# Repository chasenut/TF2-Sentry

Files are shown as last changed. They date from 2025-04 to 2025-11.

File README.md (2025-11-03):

<div align="center">

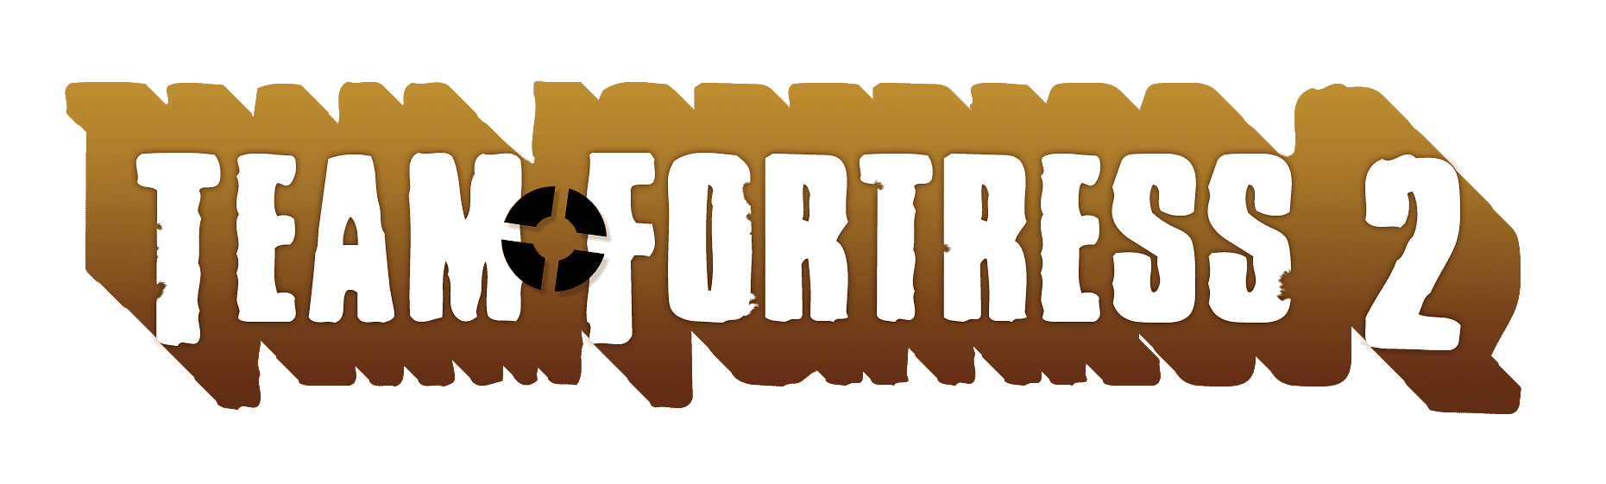
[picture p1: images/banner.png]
banner


<br>

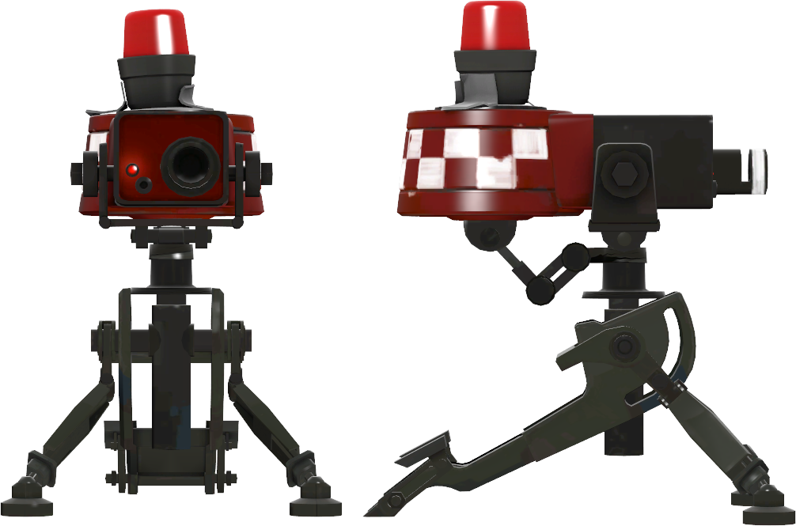
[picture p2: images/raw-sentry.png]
sentry


<br>
<br>

Team Fortress 2 Sentry (Level 1).<br>
3D print your own and upgrade it!

</div>

<br>

<div align="center">
    
# About

<br>

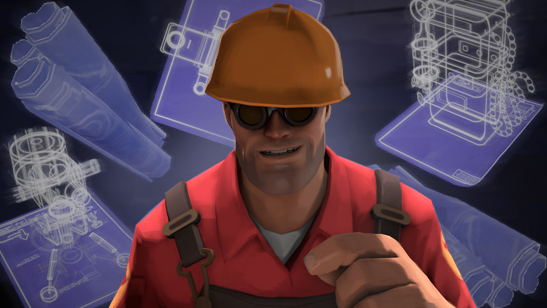
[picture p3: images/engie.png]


</div>

<br>
<br>

I started this project in February, 2025, after Valve announced open-sourcing Team Fortress 2.<br>
This is the piece of software I grew up with, so to commit something to the community, 
I made this project which includes self-made 3D CADs and some electronics. <br>
This took hundreds of hours to make, and spanned over several months to design and make.

<br>

**Feel free to do whatever you want with it!**

## Parts

Microcontroller: `esp32doit-devkit-v1`<br>
I'm using some standard servos and motors, as well as LEDs etc. <br>
All (electronic) parts can be purchased at [botland.com.pl](https://www.botland.com/pl).<br>
Everything (that could be) is 3D-printed. I made all models myself.<br>
This version of the turret 
**doesn't require any custom metal parts, everything is 3D-printable** 
and screw together using only M3 and M4 machine screws.<br>
All (printable) models should be in `parts/` directory.<br>
You can also preview the 3D model [here](https://a360.co/44RaSrK).<br>
<br>

### Needed (store bought) parts

You may need these parts:
- (3) Metal bearings `6004/2RS` (or any other model, only important thing are dimensions)
- (2) Standard servos `MG995` or `MG996R` or any standard servo that fit. **Note here**, I found these
to be a little to weak (and they don't really handle the weight of everything). I recommend finding
a stronger ones with the same dimensions
- (2) Servo horns (metal is recommended), must work with your servo, something like [these](https://www.amazon.com/Honbay-Aluminum-Standard-Airplane-Hop-up/dp/B09CT7QK6C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)
- (A lot of) `M3` and `M4` machine screws of different lengths, preferebly `10, 15, 20, 30 [mm]`
- (2) Red 8mm LED diodes
- (1) Red 6mm Laser diode (like [this](https://www.amazon.com/HiLetgo-10pcs-650nm-Diode-Laser/dp/B071FT9HSV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))
- (1) Red Siren (**to steal 2 parts nice parts from, **red transparent head** and **reflective dish**), [this one](https://www.amazon.com/Car-Siren-Strobe-Light-Rotation/dp/B0DL5T3F2J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)
- (1) Mini Motor, I used `N20-BT39 micro 1000:1 32RPM - 9V` ([mine here](https://botland.com.pl/silniki-micro-n20-seria-mp-medium-power/12601-silnik-n20-bt39-micro-10001-32rpm-9v-5904422377151.html)) 
but you may use any other of your choice (similar specs, same size), it is for siren to spin.

<br>
Of course you may also need some batteries, wires and other circuit-stuff. Not gonna lie, I didn't do the circuit stuff the best way, 
so you can definetly do better than me.

### Printing & Filaments

I used `Polymaker Polyterra` filament (1.75):
- [Matte Lava Red](https://www.amazon.com/Polymaker-PolyTerra-Bioplastic-Printing-Filament/dp/B08QMDD6NP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)
- [Matte Charcoal Black](https://www.amazon.com/Polymaker-PolyTerra-Bioplastic-Printing-Filament/dp/B08QMBPZBF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)

One spool of `red` filament is enough (1kg), but you may need a few of the `black`s, 
I used about 3-4 (kg) of those.

For **printing** I used `Bambu Lab P1S`, **no need for AMS** module. <br>
Everything is printed on `0.08 mm` layer height, I used default `Bambu Studio` presets.<br>

### Contact

For any additional info and contribution, please contanct me:

***Email***
- `switalamaciej5[at]gmail.com`

***Discord***
- `cashtan`

***Github***
- `chasenut`

## Some fun specs

This Sentry:
- Has a maximum height of about `55cm` or `21.6"`
- Is heavy (weighs a couple of solid pounds)
- Took a few (whole) days just to print the parts
- Uses many many screws
- Takes about 30-60 minutes just to dis/assemble
- Has a spinning sirent with LED
- Has a front LED and LED Laser
- Is capable of rotation:
    - vertical elevation/depression
    - horizontal traverse
- Has several moving parts

<div align="center">

# Gallery

<br>

_The white stand is not needed, it is just for display_

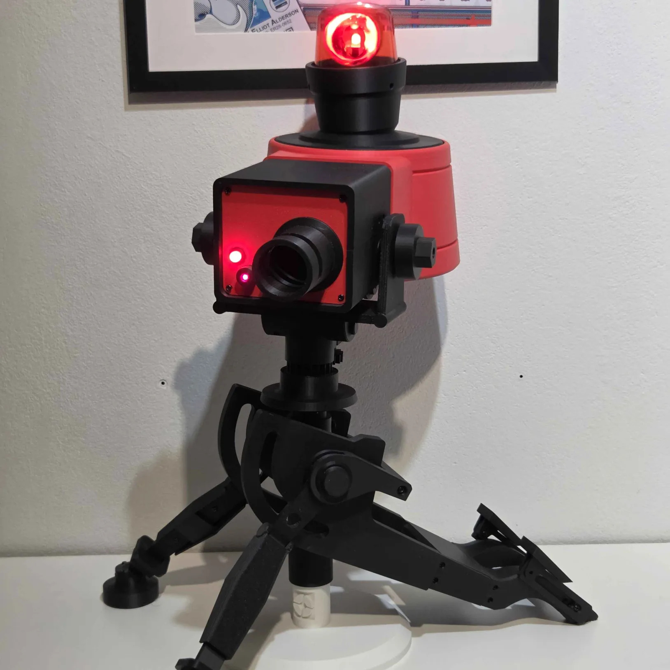
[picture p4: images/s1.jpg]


<br>

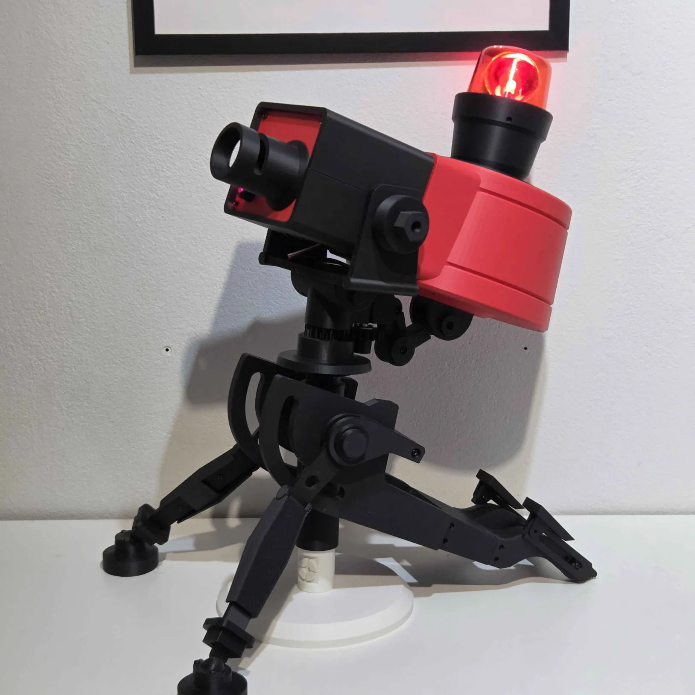
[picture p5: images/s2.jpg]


<br>

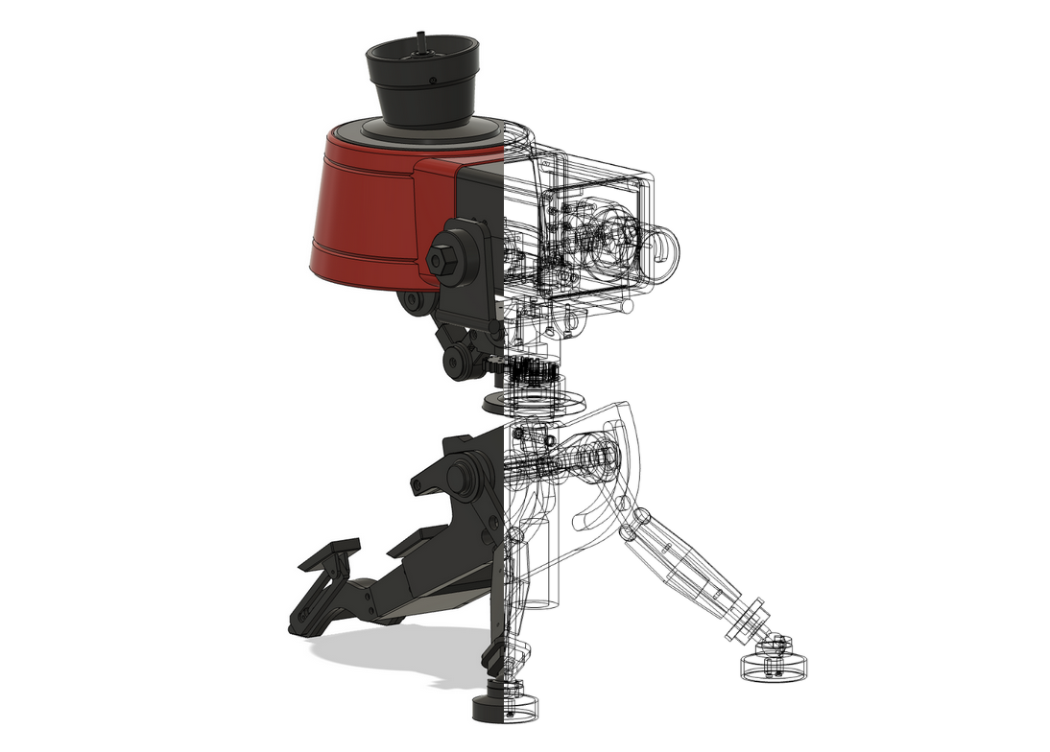
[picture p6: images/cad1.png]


</div>

<br>

# Functionality & code

This project's goal was to create a **3D replica** of Sentry from our beloved game Team Fortress 2.
Code for this Sentry _(and wireless module (Wrangler), which is not yet finished)_ isn't complete, full or outstanding, 
I would say it was just a placeholder and was assembled in a short period of time just to test the turret. **Feel free** to make/submit
your own code for this project, you can use current one as reference. 

# Code build

For building and deploying I use(d) VSC's [Platformio](https://platformio.org/).

---

<div align="center">
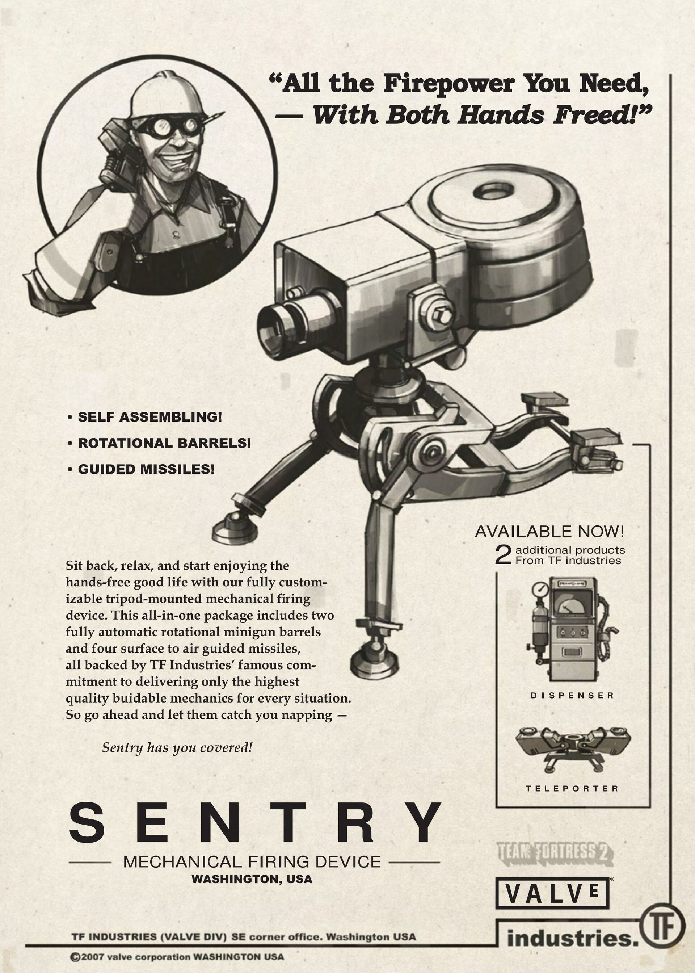
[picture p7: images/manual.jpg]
manual
    
</div>

---

## Notice

Every single parts is self-designed, none content were copied.
Inspired by [Mr. Volt](https://www.youtube.com/@MrVolt).

This project is not affiliated with Valve Corporation.
Image sources:
- [teamfortress.com](https://www.teamfortress.com)
- [mundymundy.tumblr.com](https://mundymundy.tumblr.com/post/672858009940213760/hello-can-you-do-general-relationship-headcanons)

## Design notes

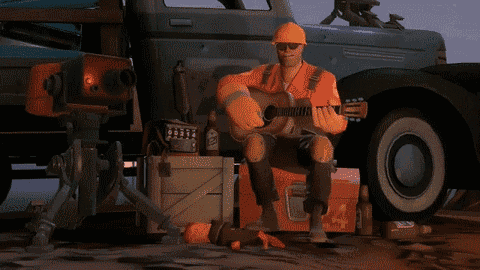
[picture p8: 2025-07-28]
images/guitar.gif

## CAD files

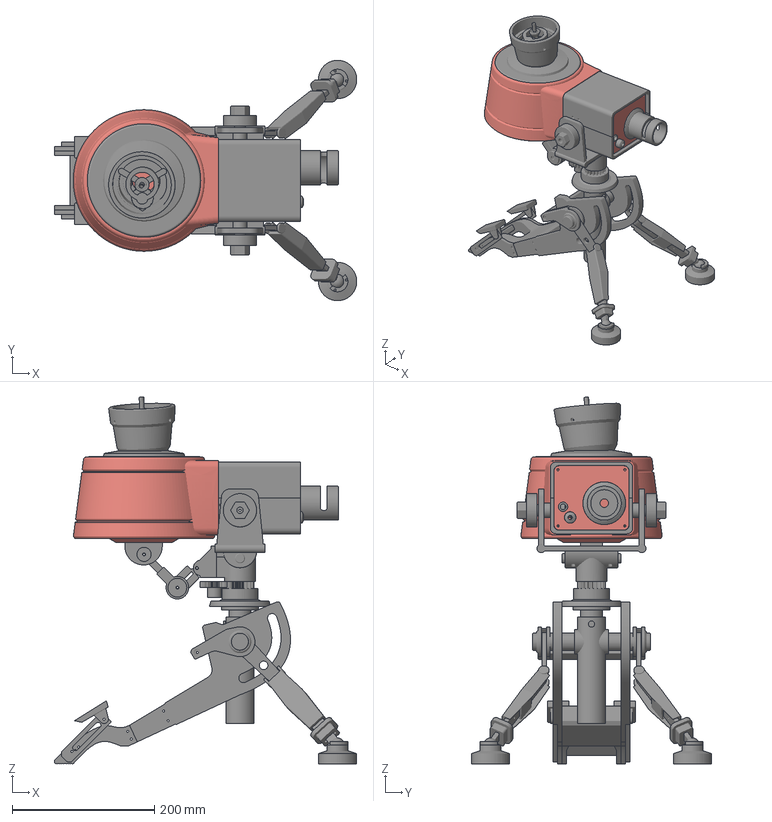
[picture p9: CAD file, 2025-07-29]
parts/TF2-Sentry-chasenut-v1-129.3mf
425.7 x 338.3 x 516.5 mm
backleg_bridge
backleg_mp_1
backleg_mp_2
backleg_smaller_bridge
backleg_sp_1
backleg_sp_2
bearing_chamber_1
bearing_chamber_2
bottom_shaft
cyl_shaft
frontleg_ball1
frontleg_ball2
frontleg_ballfence1
frontleg_ballfence2
frontleg_big_collar1
frontleg_big_collar2
frontleg_bottom1_1
frontleg_bottom1_2
frontleg_bottom2_1
frontleg_bottom2_2
frontleg_leg1
frontleg_leg2
frontleg_lower_collar1
frontleg_lower_collar2
hex_shaft
servo1_mount
servo_horn_visual
spine
thing1_1
thing1_2
thing2_1
thing2_2
up_collar1_1
up_collar1_2
up_collar2_1
up_collar2_2
up_collar_bridge
upper_shaft

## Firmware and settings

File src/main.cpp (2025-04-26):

#include <Arduino.h>
#include <WiFi.h>
#include <esp_wifi.h>
#include <esp_now.h>

// I was to lazy to make separate projects for the sentry and the wrangler
// so here are the defines
// always comment accordingly
// if not commented - build for sentry
// if commented - build for wrangler
#define DEPLOY_SENTRY

uint8_t sentry_custom_mac[] = {0xAA, 0xAA, 0xAA, 0xAA, 0xAA, 0xAA};
uint8_t wrangler_custom_mac[] = {0xBB, 0xBB, 0xBB, 0xBB, 0xBB, 0xBB};

typedef struct struct_message {
  double x_cord;
  double y_cord;
  bool btn_pressed;
} struct_message;

// Create a struct_message called myData
struct_message myData;

esp_now_peer_info_t peerInfo;


void initEspNow() {
  // Get MAC Address
  Serial.print("ESP32 Board MAC Address: ");
  Serial.println(WiFi.macAddress());
  // Init ESP-NOW
  if (esp_now_init() != ESP_OK) {
    Serial.println("Error initializing ESP-NOW");
    return;
  }
}


#ifndef DEPLOY_SENTRY
#define DEPLOY_WRANGLER
#endif

#ifdef DEPLOY_SENTRY
#include <ESP32Servo.h>

Servo xServo;
Servo yServo;
const int X_SERVO_PIN = 27;
const int Y_SERVO_PIN = 26;

const double X_SERVO_ANGLE_MAX = 180;
const double X_SERVO_ANGLE_MIN = 0;
const double Y_SERVO_ANGLE_MAX = 115;
const double Y_SERVO_ANGLE_MIN = 80;

int cycle_time = 3000;
int elapsed_time = 0;
int cycle_count = 0;

int curr_angle_x = 90; //set to 90 be default

int approx_def_joystick_offset = 1720;
int joystick_baund = 10; // offset after which things happen (like servo moves)
int joystick_ratio_comp = 1700; // what the offset from joystick is compared to
const double SENSITIVITY = 3;

int prev_t = millis();
int curr_t = millis();


// callback function that will be executed when data is received
void OnDataRecv(const uint8_t * mac, const uint8_t *incomingData, int len) {
  memcpy(&myData, incomingData, sizeof(myData));
  int x = myData.x_cord;
  int y = myData.y_cord;
  bool btn_pressed = myData.btn_pressed;
  Serial.print("Bytes received: ");
  Serial.println(len);
  Serial.print("x_cord: ");
  Serial.println(x);
  Serial.print("y_cord: ");
  Serial.println(y);
  Serial.print("btn_press: ");
  Serial.println(btn_pressed);

  int x_offset = approx_def_joystick_offset - x;
  int y_offset = approx_def_joystick_offset - y;

  if (x_offset > joystick_ratio_comp) x_offset = joystick_ratio_comp;
  if (x_offset < -joystick_ratio_comp) x_offset = -joystick_ratio_comp;
  if (y_offset > joystick_ratio_comp) y = joystick_ratio_comp;
  if (y_offset < -joystick_ratio_comp) y_offset = -joystick_ratio_comp;

  if (joystick_baund - abs(x_offset) < 0) {
    double new_angle_x = 90 + ((double)x_offset / (double)joystick_ratio_comp) * 90;
    if (new_angle_x >= X_SERVO_ANGLE_MIN && new_angle_x <= X_SERVO_ANGLE_MAX) {
      xServo.write(new_angle_x);
    }
  }

  if (joystick_baund - abs(y_offset) < 0) {

  }


}

void setup() {

  xServo.setPeriodHertz(50);
  xServo.attach(X_SERVO_PIN, 500, 2500);

  yServo.setPeriodHertz(50);
  yServo.attach(Y_SERVO_PIN, 500, 2500);

  xServo.write(curr_angle_x);
  yServo.write(90);

  Serial.begin(9600);

  // ESPNow STUFF
  WiFi.mode(WIFI_STA);
  esp_wifi_set_mac(WIFI_IF_STA, sentry_custom_mac);
  initEspNow();
  // Once ESPNow is successfully Init, we will register for recv CB to
  // get recv packer info
  esp_now_register_recv_cb(OnDataRecv);


  delay(3000);
}


void loop() {
  elapsed_time = millis();
  //Serial.println("millis: " + String(elapsed_time));
  cycle_count = floor(elapsed_time / cycle_time);
  //Serial.println("cycle_count: " + String(cycle_count));
  bool dir = cycle_count % 2 == 0 ? true : false;
  //Serial.println("dir: " + String(dir));
  double ratio = (double)(elapsed_time % cycle_time) / (double)cycle_time;
  double angle = dir ? ratio * 180 : 180 - ratio * 180;
  //Serial.println("angle: " + String(angle));
  //xServo.write(angle);


  if (Serial.available() > 0) {
    String input = Serial.readStringUntil('\n');
    double angle = input.toDouble();
    if (angle >= 85 && angle <= 105) {
      yServo.write(angle);
    }
    Serial.println("\nEnter Servo value: ");
  }
}
#endif

#ifdef DEPLOY_WRANGLER

const int JOY_X_PIN = 32;
const int JOY_Y_PIN = 35;
const int JOY_BTN_PIN = 34;

// callback when data is sent
void OnDataSent(const uint8_t *mac_addr, esp_now_send_status_t status) {
  //Serial.print("\r\nLast Packet Send Status:\t");
  //Serial.println(status == ESP_NOW_SEND_SUCCESS ? "Delivery Success" : "Delivery Fail");
}


void setup() {

  Serial.begin(9600);

  // ESPNow STUFF
  WiFi.mode(WIFI_STA);
  esp_wifi_set_mac(WIFI_IF_STA, wrangler_custom_mac);
  initEspNow();
  // Once ESPNow is successfully Init, we will register for Send CB to
  // get the status of Transmitted packet
  esp_now_register_send_cb(OnDataSent);

  // Register peer
  memcpy(peerInfo.peer_addr, sentry_custom_mac, 6);
  peerInfo.channel = 0;  
  peerInfo.encrypt = false;

  if (esp_now_add_peer(&peerInfo) != ESP_OK){
    Serial.println("Failed to add peer");
    return;
  }

  // Pins
  pinMode(JOY_BTN_PIN, INPUT_PULLUP);

}

void loop() {

  int joy_x_val = analogRead(JOY_X_PIN); //  0–4095
  int joy_y_val = analogRead(JOY_Y_PIN); //  0–4095
  bool joy_btn_pressed = digitalRead(JOY_BTN_PIN) == LOW;

  // Set values to send
  //strcpy(myData.someString, "THIS IS A CHAR");
  myData.x_cord = joy_x_val;
  myData.y_cord = joy_y_val;
  myData.btn_pressed = joy_btn_pressed;
  
  // Send message via ESP-NOW
  esp_err_t result = esp_now_send(sentry_custom_mac, (uint8_t *) &myData, sizeof(myData));
   
  if (result == ESP_OK) {
    Serial.println("Sent with success");
  }
  else {
    Serial.println("Error sending the data");
  }
  //delay(20);
}

#endif
